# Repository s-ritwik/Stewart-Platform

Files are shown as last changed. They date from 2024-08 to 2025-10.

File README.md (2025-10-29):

# Ship Motion Mimicking and Self-Stabilizing Platform Project


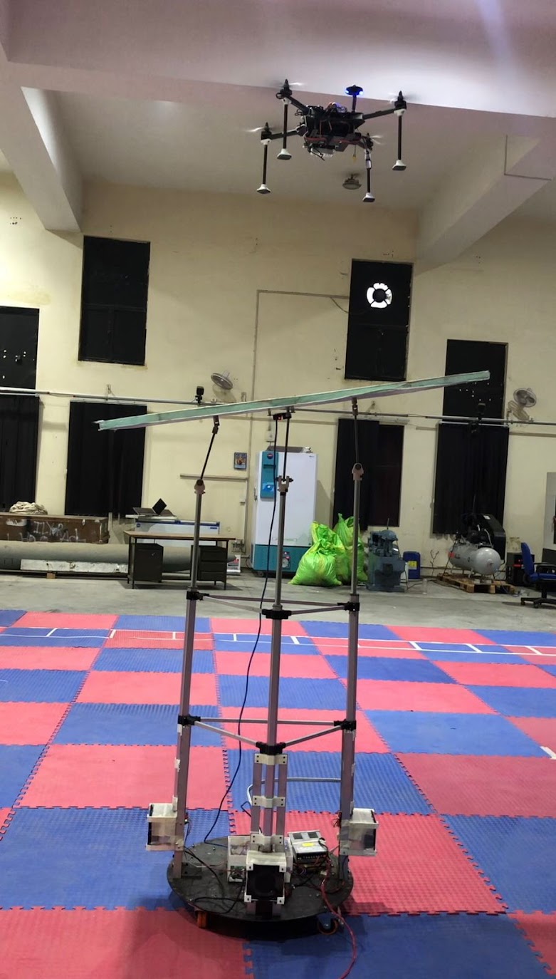
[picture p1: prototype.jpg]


## Overview
This is my undergraduate project aimed at mimicking ship motion and developing a self-stabilizing platform. The project focuses on accurately replicating the dynamic movements of a ship and ensuring that the platform remains stable under various simulated conditions.

## Project Components
- **Ship Motion Mimicry**: Implementing algorithms to replicate the motion dynamics of a ship.
- **Self-Stabilizing Platform**: Designing and testing a platform that can counteract motion to remain stable.
- **CAD Models**: Detailed CAD models of the platform and associated components are available for reference.

## Available Resources
- **[Project Report](Stewart_Platform_1.pdf)**: A comprehensive report detailing the project’s objectives, methodologies, and results.
- **[CAD Models](CAD2.0)**: Access the CAD models used in this project.

## Future Updates
The final pipeline, including Arduino/Raspberry Pi integration, will be posted soon after concluding all tests.

## How to Contribute
Contributions are welcome! Feel free to fork the repository and submit pull requests. If you have any questions or suggestions, please open an issue.

## License
This project is licensed under the Apache License - see the [LICENSE](LICENSE) file for details.

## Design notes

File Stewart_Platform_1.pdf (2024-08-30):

# Project Report:Design and fabrication of Stewart platform for Testing of UAV Ship Deck Landing

Abhishek∗

, Ritwik Shankar†

, Jitendra Singh‡

I. Nomenclature
R | = Radius of the stewart platform
Z | = Heave value considered from ground point
la | = Deflection of the aft actuator from ground point
l f | = Deflection of the forward actuator from ground point
ll | = Deflection of the lateral actuator from ground point
θ | = Pitch deflection of the platform along y axis
φ | = Roll deflection of the platform along x axis
ax | = Raw acceleration data along x axis from MPU6050
ay | = Raw acceleration data along y axis from MPU6050
az | = Raw acceleration data along z axis from MPU6050

θ

accel = Pitch deflection from acceleration data
φ
accel | = Roll deflection from acceleration data
wx | = Angular velocity along x axis
wy | = Angular velocity along y axis
wz | = Angular velocity along z axis
α | = Complimentary filter value

II. Introduction

A. Problem Statement
The challenge of landing a rotor-craft on the deck of a moving ship presents a complex problem that requires precise piloting skills and specialized training. The continuous pitching and rolling of the ship’s deck, driven by ocean swells and winds, creates an inherently unstable landing platform that challenges the pilot’s ability to time the touchdown precisely. The limited physical dimensions of the ship’s deck provide a little margin for error, requiring the pilot to execute the landing manoeuvre with exceptional precision within the constrained spatial envelope. The airflow patterns around the ship’s superstructure and the interaction with the surrounding marine environment can result in turbulent and unpredictable wind conditions, further complicating the pilot’s control inputs.
Successful ship deck landings demand the ability to accurately anticipate the ship’s motion and synchronize the aircraft’s descent. This requires specialized skills, such as precise control inputs to compensate for platform instability, keen situational awareness to monitor the landing environment, and rapid decision-making to address unexpected events. In this paper we investigate a solution to these problems by using vision based estimation of the ship deck platform then a landing algorithm which achieves precision landing on a rolling and pitching platform. To solve this problem, a control algorithm was developed using position estimates from computer vision data. To test the algorithm, a Parallel manipulator was developed, which can accurately simulate ship motions such as roll, pitch and heave, giving a 3-DOF motion to the landing plate. This type of parallel manipulator is known as a Stewart Platform.
B. Literature Review
Ready-made Stewart Platforms were inquired about, but those that fit our requirements were priced above INR 40 Lakhs. Consequently, creating an in-house alternative to cater to our required ship motions became necessary. The

∗Professor, Aerospace Engineering, Indian Institute of Technology Kanpur, Uttar Pradesh, India, 208016, AIAA Member
†Under-Graduate Student, Aerospace Engineering, Indian Institute of Technology Kanpur, Uttar Pradesh, India, 208016
‡Senior Project Executive Officer, Aerospace Engineering, Indian Institute of Technology Kanpur, Uttar Pradesh, India, 208016 dynamics of a Stewart platform were explored through the examination of two sources ([1] & [2]). These sources were consulted to gain insight into the mechanics and functioning of the Stewart platform

III. Ship Deck Simulation Platform

A. Introduction to Stewart Platform
A Gough-Stewart platform was planned to replicate the scone ocean dataset. The anticipated versatility of the Stewart platform for stabilizing ships at sea is illustrated in Fig. 1.

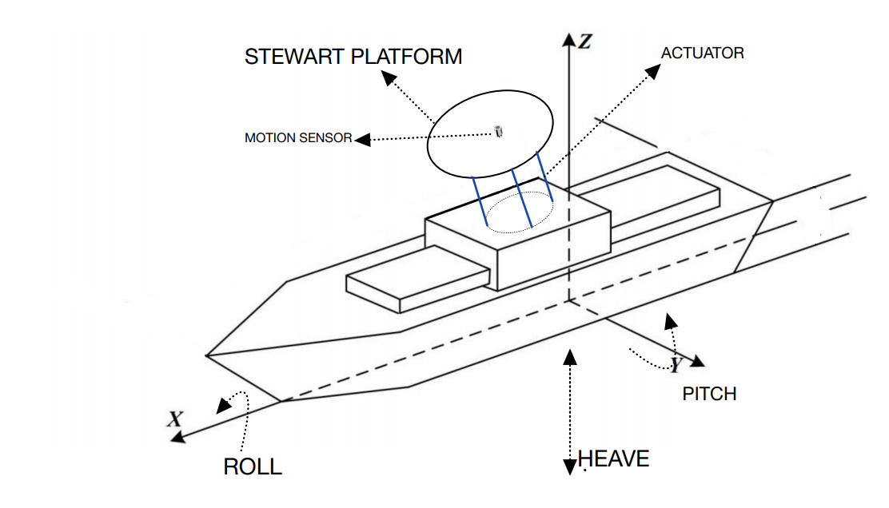
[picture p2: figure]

Fig. 1 The broad applicability of the Stewart platform for stabilizing ships at sea.

Rather than stabilizing the shipboard directly, in our experiment experimentally taken ship data [3] was inputted into the platform to simulate ship conditions at sea state 4 [4].
The aim was to simulate roll(φ),pitch(θ) and heave(Z) motions to test the landing algorithm, as these are the most significant motions captured in the scone dataset; other motions in the plane of the ocean can be mimicked by keeping the platform on a car, which can move in the two perpendicular directions on the ground and also rotate around the axis perpendicular to the plane. Existing market platforms, albeit with a higher frequency operating range, were priced at over 40 Lakhs INR. Hence, there was a significant demand for a cost-effective alternative to a Stewart platform capable of generating the desired motions at a lower frequency of approximately 10 Hertz.
The SCONE dataset [3], acquired through experimentation, was slated for simulation. This dataset comprises two distinct types of data: one predominantly influenced by roll and the other by heave. It is structured as a MATLAB variable containing 36,000 data points, with a time interval of 0.05 seconds between consecutive points. Our research focuses on testing our algorithm using both the roll-dominated and Heave-dominated subset of this dataset (‘SCONE_D3R_1‘ and ‘SCONE_D3H_1‘), where ‘Rot_X‘ represents roll, ‘Rot_Y‘ represents pitch, and Z represents heave. The deck is situated 15 feet (Z = -15 feet) above sea level (Z = 0). The data which is to be simulated is shown in Fig. 2.

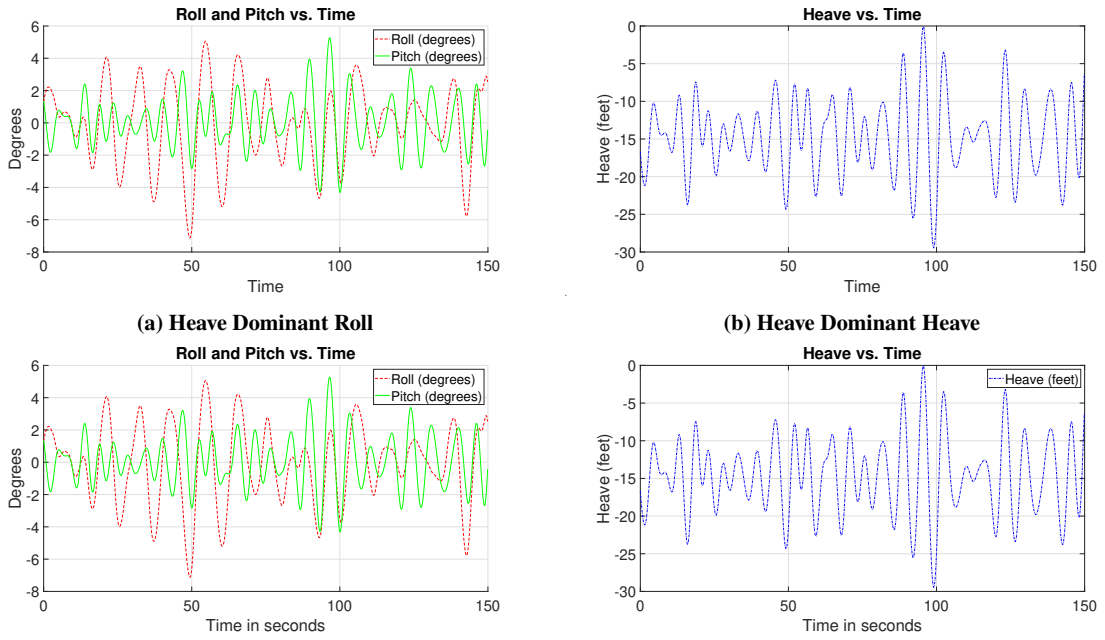
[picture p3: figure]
Time; Degrees; Roll and Pitch vs. Time; Roll (degrees) Pitch (degrees); (a) Heave Dominant Roll; Heave (feet); Heave vs. Time; (b) Heave Dominant Heave; Time in seconds

(c) Roll Dominant Roll
(d) Roll Dominant Heave

Fig. 2 Comparison of Heave and Roll Dominant Parameters

B. Kinematics of the 3-legged platform

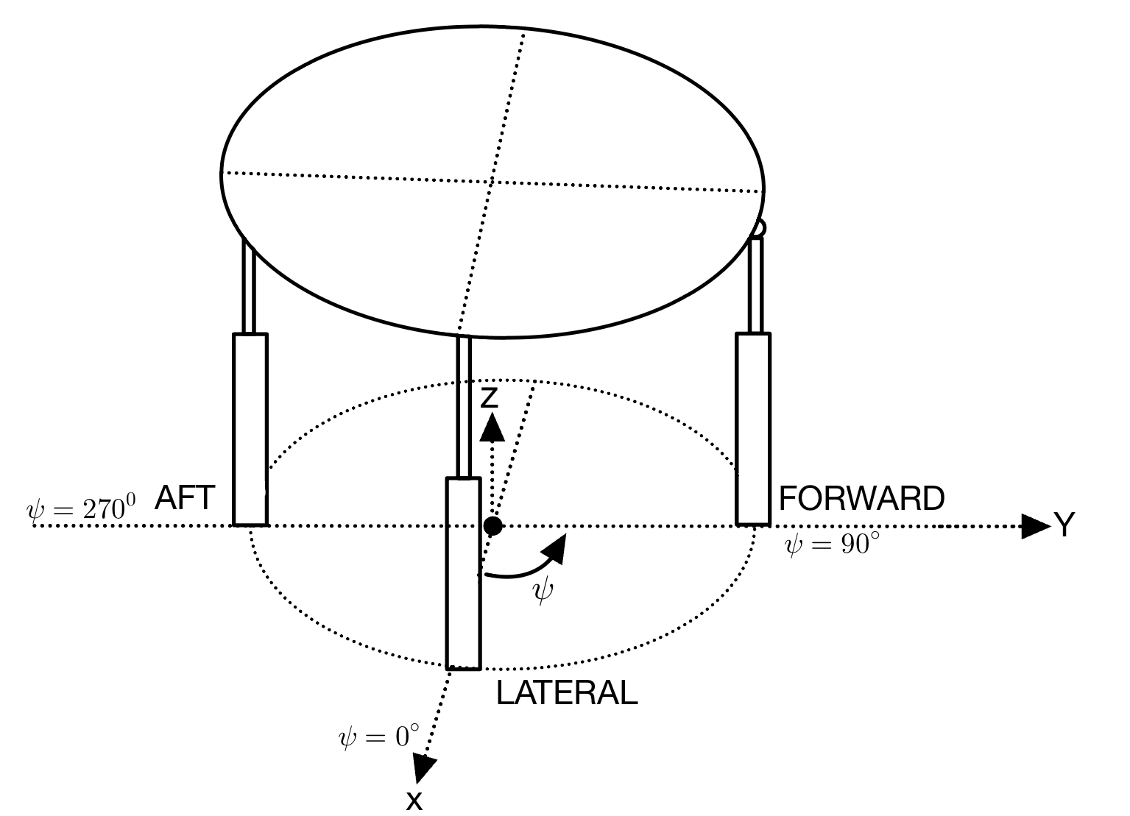
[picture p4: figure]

Fig. 3 Proposed design of the model

Given that actuators constituted the majority of the cost, reducing their number was crucial. Drawing inspiration from UH-60A swashplate [5], a 3-actuator model was chosen for the platform. Since the design drew inspiration from a swashplate, a similar naming convention was adopted for the three actuators: ’lateral’, ’aft’, and ’forward’. In this configuration (Fig. 3), the lateral actuator generates pitching movement, while the aft and forward actuators produce rolling movement.

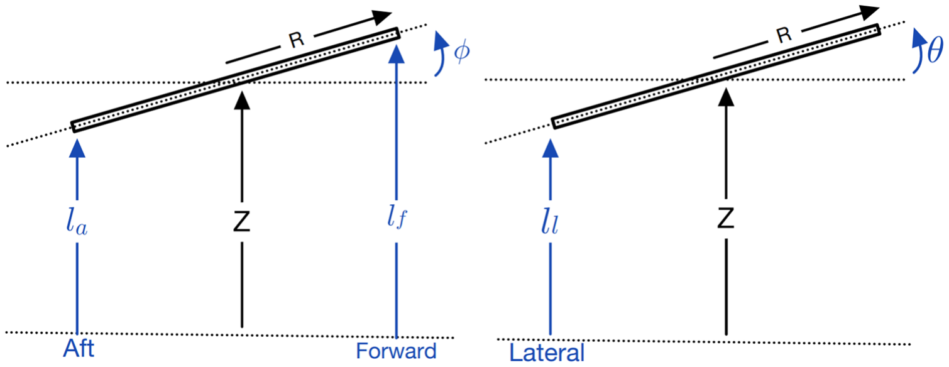
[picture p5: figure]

Fig. 4 Deflection diagram of the system

The inverse kinematics (Fig.4) of the system were solved to determine the necessary movements (Eq. 1) of the actuators to achieve the desired roll, pitch, and heave motions. This process allowed for precise control over the platform’s movements to accurately simulate the conditions needed for testing the landing algorithm.

la = Z − R sin(φ) AFT
l f = Z + R sin(φ) | FORWARD
ll = Z − R sin(θ) | LATERAL

(1)

C. Design of the platform
The decision was made to combine a hinge joint and a universal joint instead of using a three-degree-of-freedom ball joint to allow the top plate to rotate freely around the two desired axes while ensuring it can withstand significant loads. This resulted in adopting a linear actuator-hinge joint-universal joint setup, with the universal joint affixed to the top plates for all three actuators. Mechanical components were carefully chosen based on their functionality and cost considerations.
A linear actuator with an optical encoder to get deflection was chosen with a 6-inch stroke length to accommodate the needs of roll, pitch and heave adequately. The linear speed was 2 inches per second with a load capacity of 36 pounds(16.32 Kg) and a backtracking limit of 200 pounds(90.71 Kg) powered by a 12V SMPS box for power supply. The distance of the three actuator cuts from the centre was 30 cm, which could give us a deflection of approximately 10 degrees in under a second.
Keeping these configurations in mind, a CAD model was created for precision plasma cut for the base plate of the platform so that the actuators can be fixed on the base plate (Mild steel) with precision.

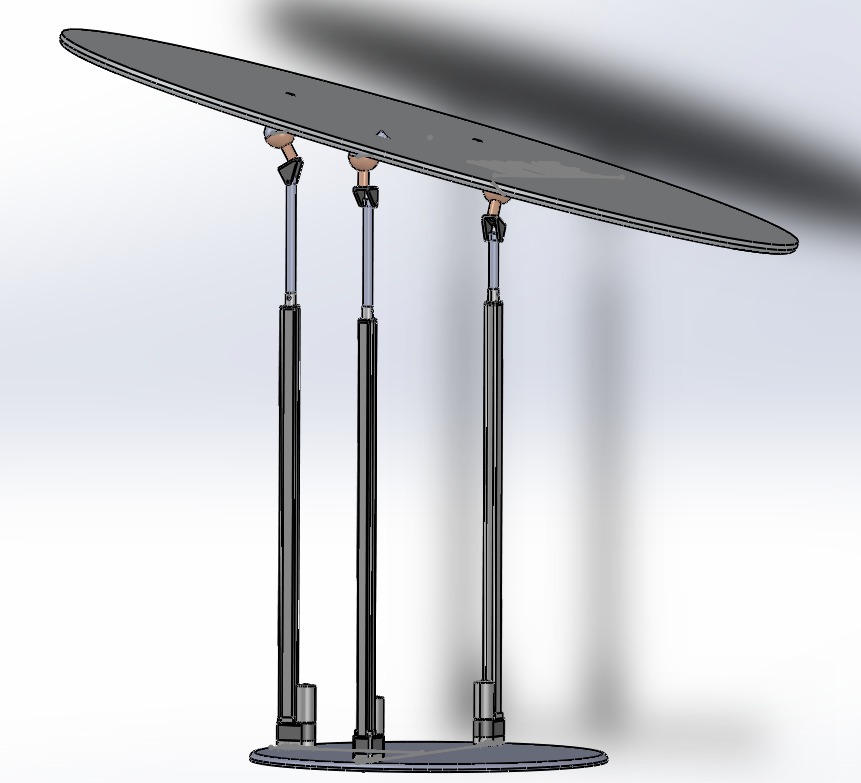
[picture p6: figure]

Fig. 5 Platform’s final Configuration

D. State estimation & Controller design
The MPU6050 IMU sensor was utilized to capture raw acceleration and gyroscope data from the platform.It was attached at the centre of the top plate of the platform. The accelerometer and gyroscope biases are calculated as zero offsets by keeping the IMU stationary and flat on level ground. For the scale factor of the accelerometer, we solve the system of linear equations for three known orientations. As described in ([6]) the euler angles, roll(φ) and pitch(θ) from acceleration readings are calculated as follows:

φ

accel = tan−1

ay

az

(2)

θ

accel = tan−1

−ax
√︁
(ay)

2 + (az )

2

!
(3)

Before discussing the calculation of the final euler angles, it is important to understand the context and objectives of our data collection methods.
- Gyroscope data furnishes rapid response and high-frequency details regarding orientation changes, albeit prone to drift over time.
- Accelerometer data delivers precise insights into gravity’s direction but is vulnerable to noise and inaccuracies in an actuated system, particularly during motion.
Employing a blending factor of 0.9, the complementary filter ([7]) combines the gyroscopic and acceleration data to compute the final pitch and roll values. At each iteration, a new roll(Eq.4) and pitch(Eq.5) are determined, factoring in the difference in time (dt) between consecutive iterations.

φ = α · (φ + wx · dt) + (1 − α) · φ

accel | (4)

θ = α · (θ + wy · dt) + (1 − α) · θ

accel | (5)

The Heave calculation for the platform is determined by pose estimation using an ArUco marker and a webcam. The control architecture of the full system is given in Fig. 6

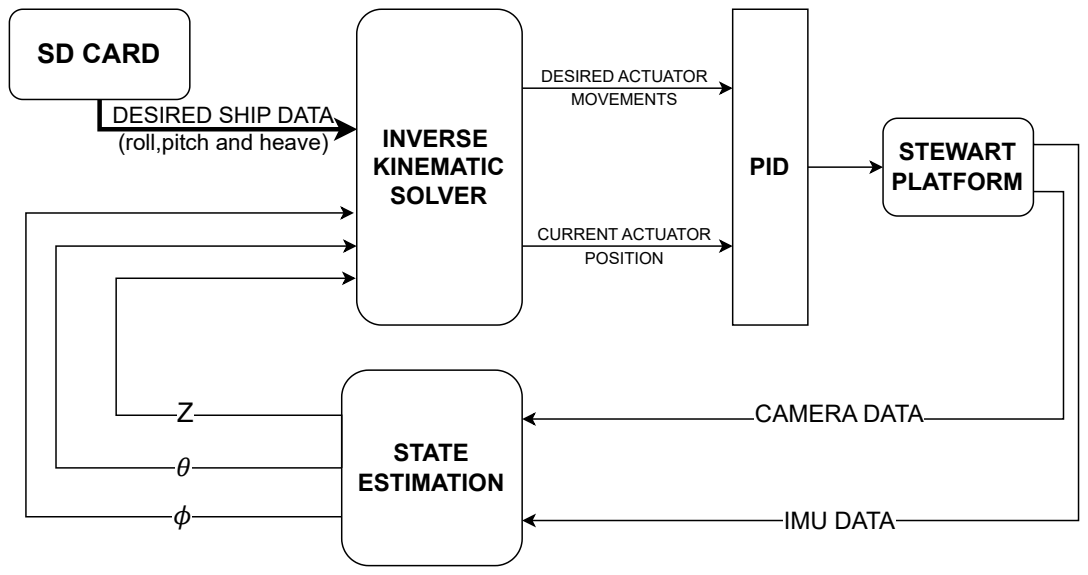
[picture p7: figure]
SD CARD; DESIRED ACTUATOR; INVERSE KINEMATIC SOLVER; IMU DATA; CAMERA DATA; STEWART PLATFORM; STATE ESTIMATION; PID; MOVEMENTS; CURRENT ACTUATOR POSITION; DESIRED SHIP DATA (roll,pitch and heave)

Fig. 6 Control architecture of the system

E. Hardware Implementation

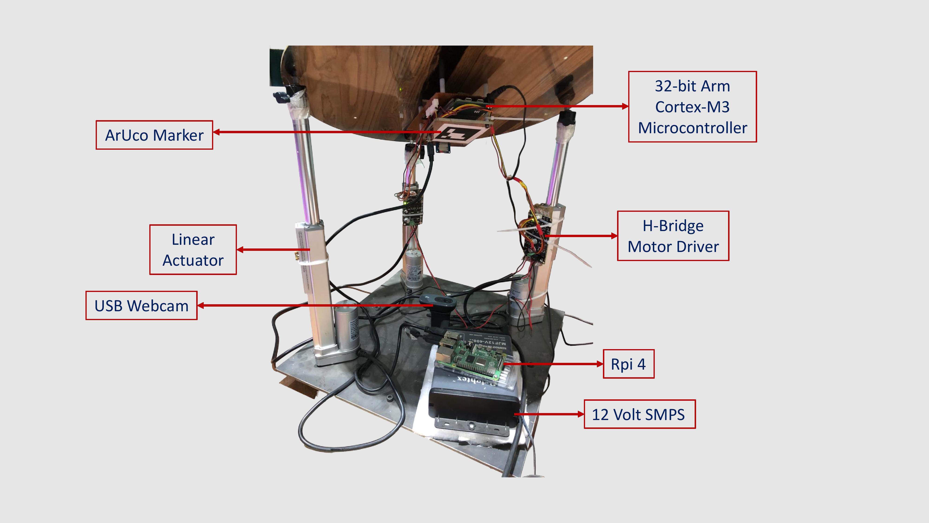
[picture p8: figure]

Fig. 7 Electronic components of the system

The platform’s electronics, illustrated in Fig. 7, includes an MPU6050 sensor, which collects raw accelerometer and gyroscopic data and transmits it to an Arduino Due microcontroller based on the 32-bit Atmel SAM3X8E ARM Cortex-M3 CPU. This microcontroller performs inverse kinematics calculations and controls the linear actuators to achieve the desired lengths using the Cytron Dual Channel Enhanced 10Amp DC Motor Driver 30A Peak MDD10A, which features an H-bridge and is powered by a 12 Volt 100A SMPS board. A Quad-core Cortex-A72 (ARM v8) 64-bit Raspberry Pi 4 processes ArUco marker data from a USB webcam to determine the distance from the bottom plate to the board (Z, or heave) and receives Qualisys motion capture data via a master-slave link, with the Qualisys system as the master and the Raspberry Pi 4 as the slave. An SD card provides the microcontroller with reference ship sea state data and logs the resulting platform data. The overall hardware architecture of the platform is detailed in Figure 8.

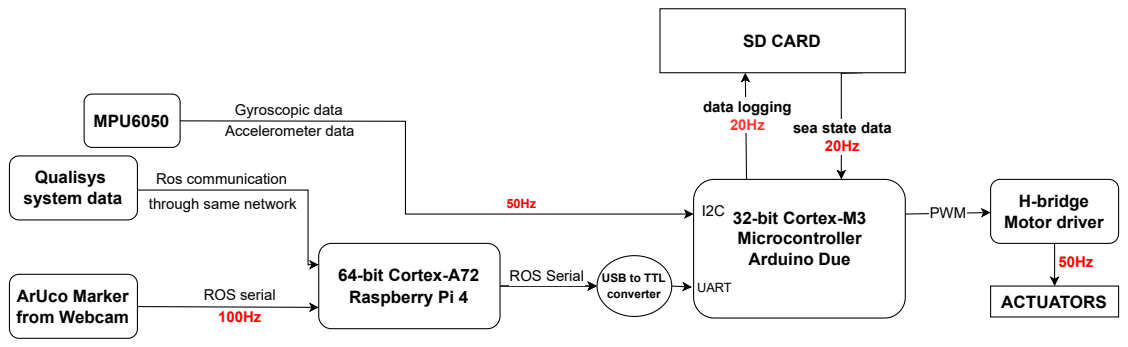
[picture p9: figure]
32-bit Cortex-M3; PWM; Microcontroller Arduino Due; H-bridge Motor driver; sea state data 20Hz; SD CARD; data logging 20Hz; Gyroscopic data Accelerometer data; MPU6050; 64-bit Cortex-A72 Raspberry Pi 4; USB to TTL converter; Qualisys system data; ArUco Marker from Webcam; ACTUATORS; ROS Serial; UART; Ros communication; through same network; ROS serial 100Hz

Fig. 8 Hardware architecture of the system

F. Results

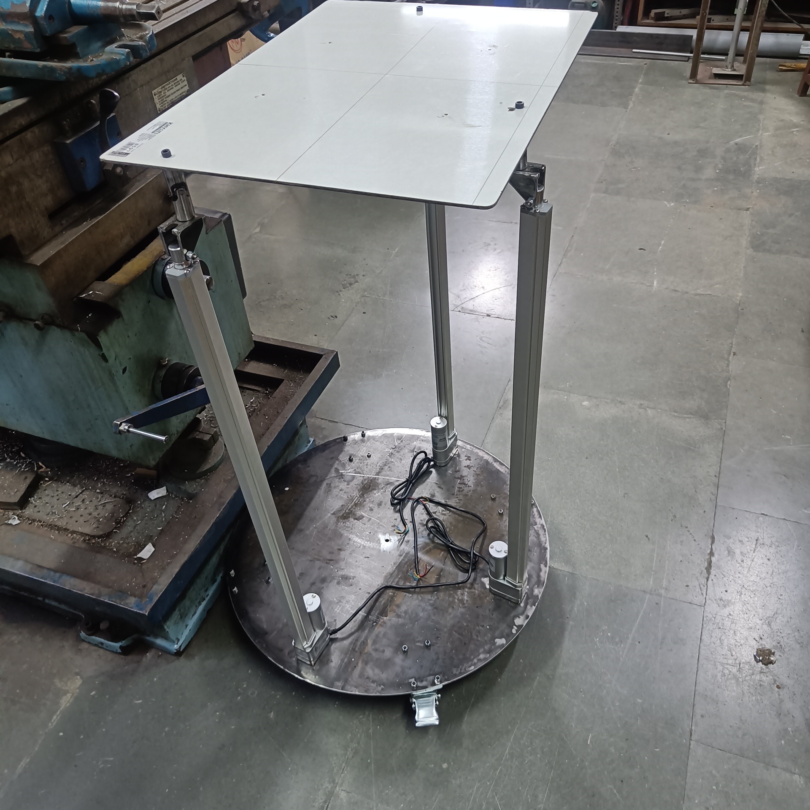
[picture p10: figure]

Fig. 9 Stewart Platform Assembly

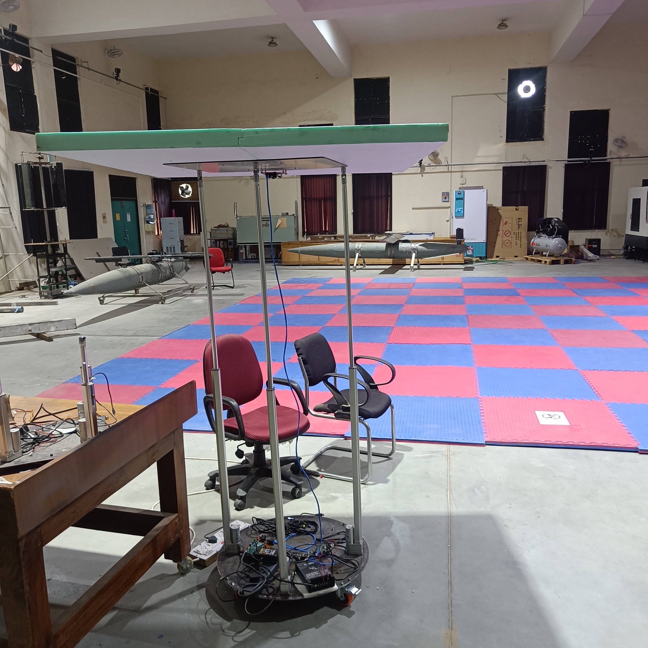
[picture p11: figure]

Fig. 10 Final Stewart Platform

The base plate was constructed and actuators were assembled (Fig. 9), with a top plate made of XPS foam board attached to the three actuators, chosen for its lightweight properties and minimal bending, which helps reduce vibrational noise affecting the IMU sensor. A Qualisys motion capture system was set up, and five super spherical markers were placed on the platform for accurate motion tracking. The final setup is illustrated in Fig. 10.
To evaluate the platform’s functionality, the Scone dataset was loaded onto the platform. The tracked values from the IMU, ArUco marker, and motion capture system were compared against the reference values for the roll(Fig. 11). Additionally, the sinusoidal data tracked by the ArUco marker and motion capture system was compared to the reference values for heave(Fig. 12).

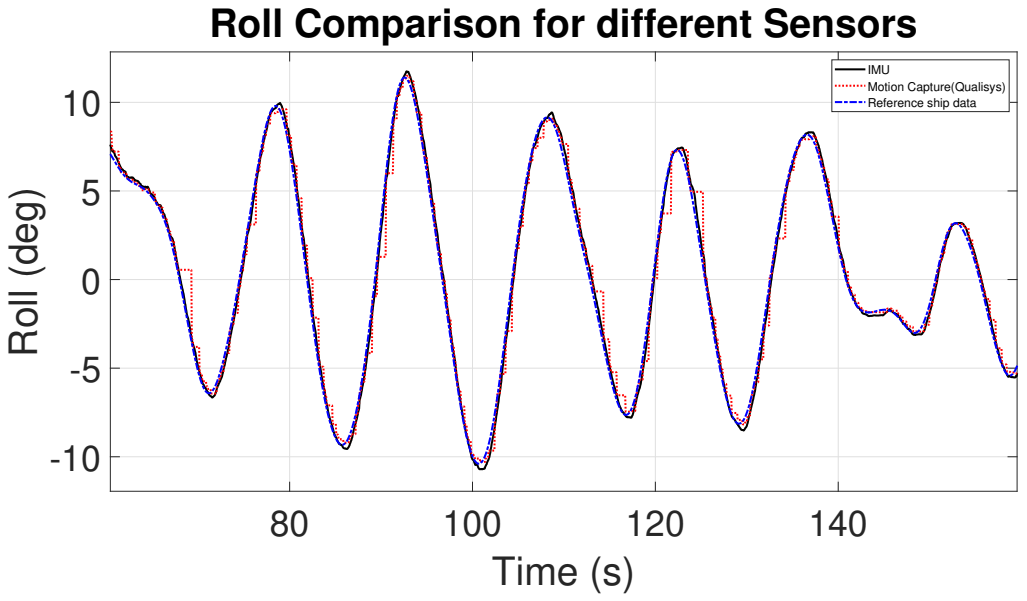
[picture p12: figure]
Time (s); Roll (deg); Roll Comparison for different Sensors; IMU Motion Capture(Qualisys) Reference ship data

Fig. 11 Roll data performance of the platform

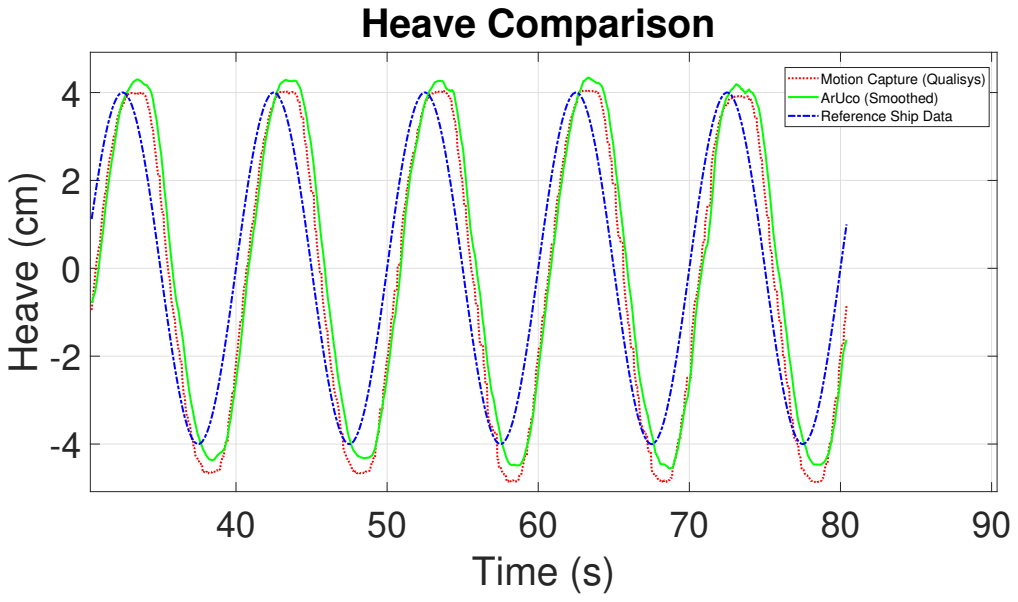
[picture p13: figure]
Time (s); Heave (cm); Heave Comparison; Motion Capture (Qualisys) ArUco (Smoothed) Reference Ship Data

Fig. 12 Heave data performance of the platform

IV. Future Work

A. Linear Speed
The first iteration model was successfully able to cater for the needs of Roll/Pitch or Heave, but when all three motions were combined, it was not able to follow the data with the precision that we wanted.So, increasing the speed of the linear actuators was necessary. The faster motors, which is rated for 22 Volts, have been ordered, and the gear assembly of the Linear actuator has been changed by using a custom 3D Printed Gear assembly and increasing the ratio from the initial 5:1 to 1:1.6, increasing the speed 8.33 times. We expect a further increase in linear speed after replacing the actuator motors. The motors have arrived and the final assembly is to be completed by 10th August.
B. Additional Degrees of Freedom
To test the algorithm for a more realistic condition, additional movements of Sway are to be added as well,this will be achieved by TO BE ADDED

References
[1] Staicu, S., “Dynamic analysis of the 3-3 Stewart platform,” UPB Scientific Bulletin D, Vol. 71, No. 2, 2009, pp. 3–18.
[2] Abedinnasab, M. H., Yoon, Y.-J., and Zohoor, H., “Exploiting higher kinematic performance-using a 4-legged redundant PM rather than gough-stewart platforms,” Serial and Parallel Robot Manipulators-Kinematics, Dynamics, Control and Optimization, Vol. 10, 2012, p. 32141.
[3] Schwartz, A., “Systematic Characterization of the Naval Environment (SCONE) - Standard Deck Motion Data for a Generic Surface Combatant,” [Online]. Available: http://www.navalengineers.org/Symposia/PastSymposia/Launch-and-Recovery-2016/Program/Schwartz, (http://www.navalengineers.org/Symposia/PastSymposia/Launch-and-Recovery-2016/Program/Schwartz) 2015.
[4] Owens, E. H., SEA CONDITIONSDouglas scale; Peterson scale; Sea stateSea conditions, Springer US, New York, NY, 1984, pp. 722–722. https://doi.org/10.1007/0-387-30843-1_397, URL https://doi.org/10.1007/0-387-30843-1_397.
[5] Abhishek, A., Datta, A., and Chopra, I., “Prediction of UH-60A structural loads using multibody analysis and swashplate dynamics,” Journal of aircraft, Vol. 46, No. 2, 2009, pp. 474–490.
[6] Kharolia, D., Singh, J., and Kothari, M., “Autopilot Design and Development for Multirotor UAVs,” AIAA SCITECH 2024 Forum, 2024, p. 1698.
[7] Van de Maele, P.-J., “Reading a imu without kalman: The complementary filter,” Pieter-Jan. com Creaty in Automation y More, Vol. 26, 2013.

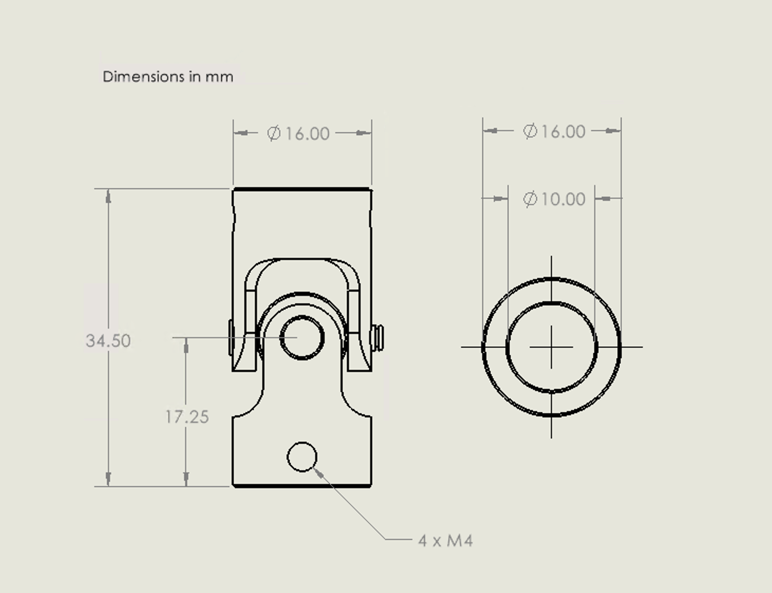
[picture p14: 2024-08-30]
CAD2.0/universal/Images/dimensions.png

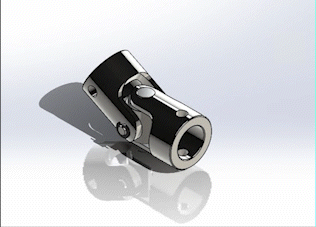
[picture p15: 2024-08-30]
CAD2.0/universal/Images/exploded.gif

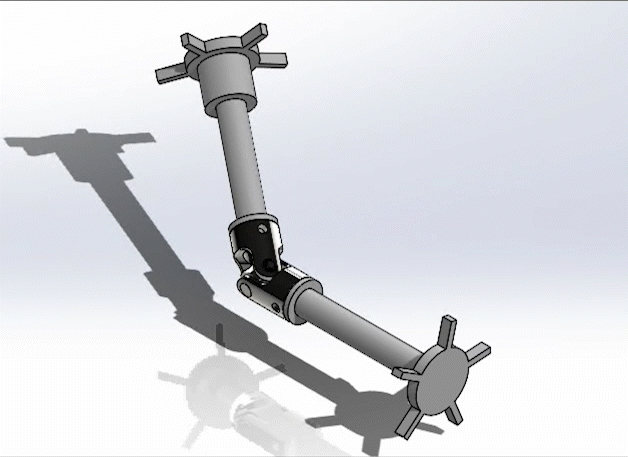
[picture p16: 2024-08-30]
CAD2.0/universal/Images/action.gif

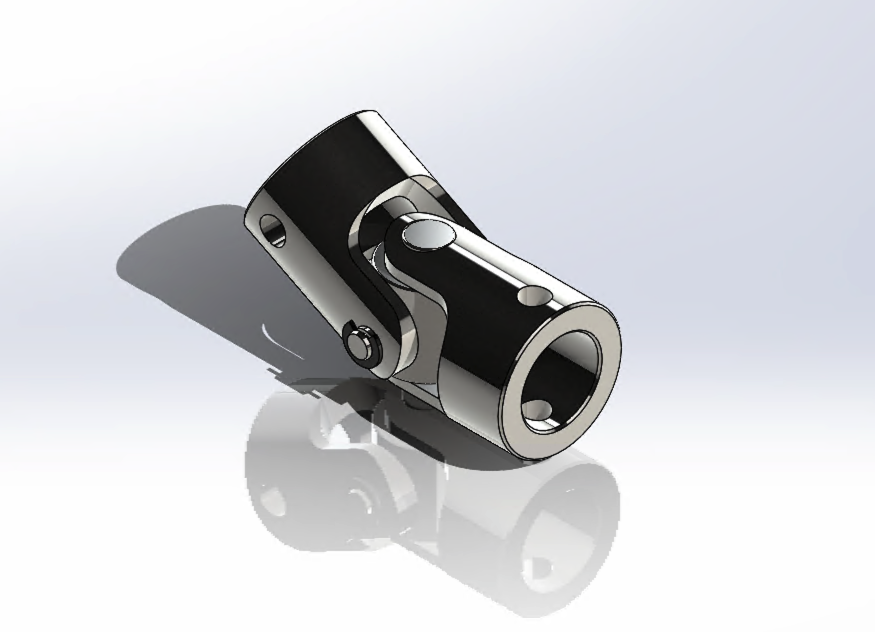
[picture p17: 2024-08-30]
CAD2.0/universal/Images/CAD.png

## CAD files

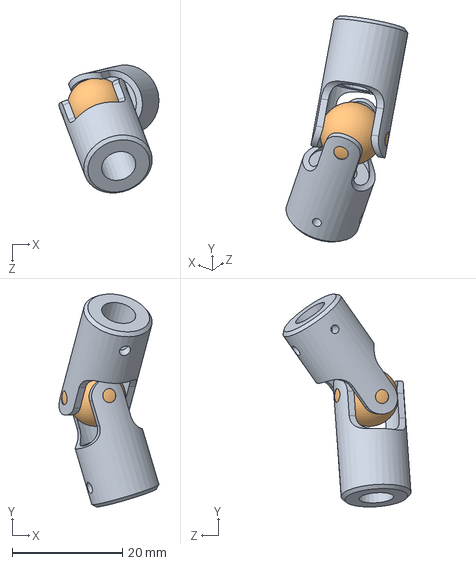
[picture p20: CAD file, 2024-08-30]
CAD2.0/uni/ASSY_BERG_UJ3_U-JOINT_0250 SHAFT.sldasm
18.1 x 38.6 x 23.1 mm
UJ-3_YOKE x 2
UJ-3_BALL

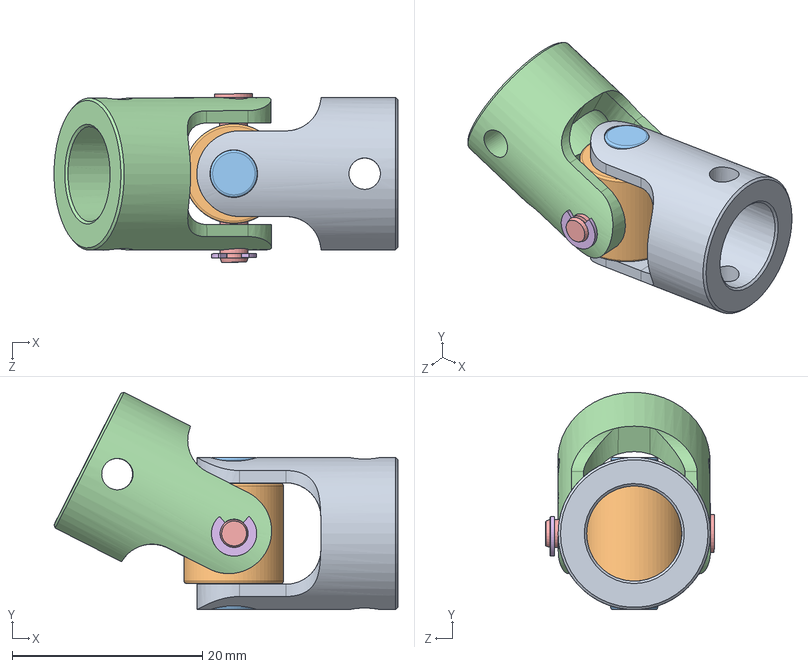
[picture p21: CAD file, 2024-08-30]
CAD2.0/UniversalJoint_10x10mm.SLDASM
36.1 x 22.8 x 17.7 mm
ForkA
Center
PinA
ForkB
PinB
Tab

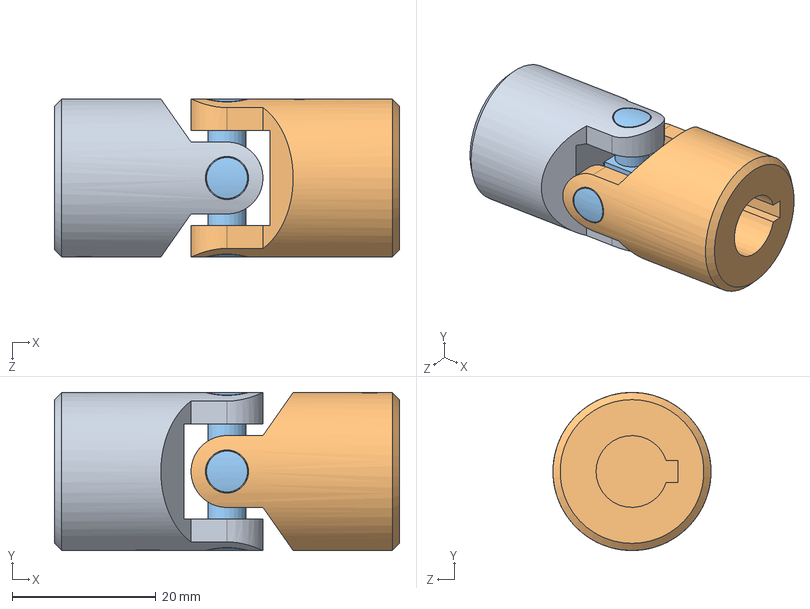
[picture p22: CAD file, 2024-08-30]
CAD2.0/03H-N_assembly/T.E.A. Transmissions Pty Ltd - Australia b65f3cdd-ef4a-384b-a0e4-523af0b97be2.SLDASM
48.0 x 22.0 x 22.0 mm
03h-n_01
03h-n_02
03h-n_03

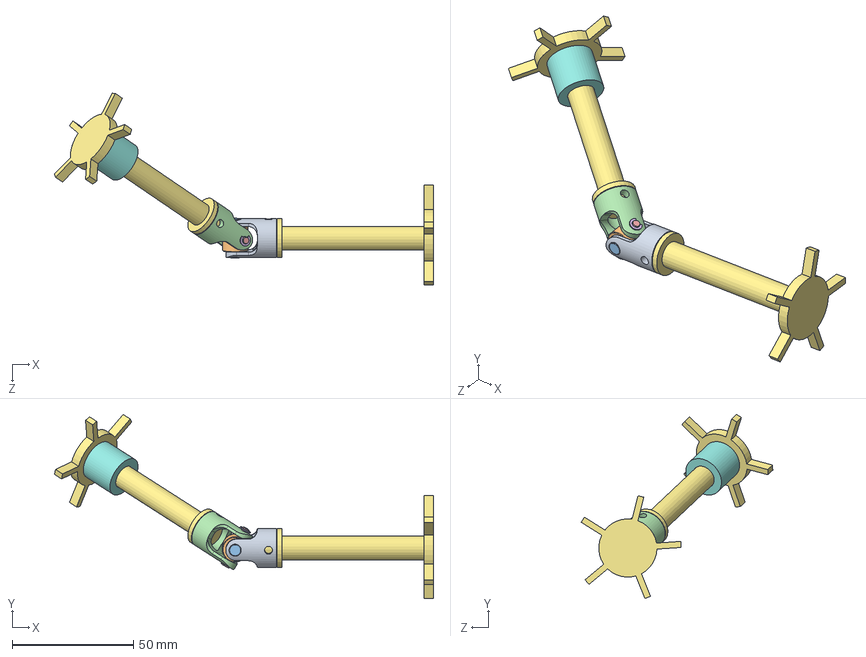
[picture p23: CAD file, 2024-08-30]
CAD2.0/universal/SolidWorks/Sample Assembly/SampleAssembly.SLDASM
156.2 x 75.9 x 79.0 mm
ForkA
Center
PinA
ForkB
PinB
Tab
SampleRod x 2
SampleCoupling

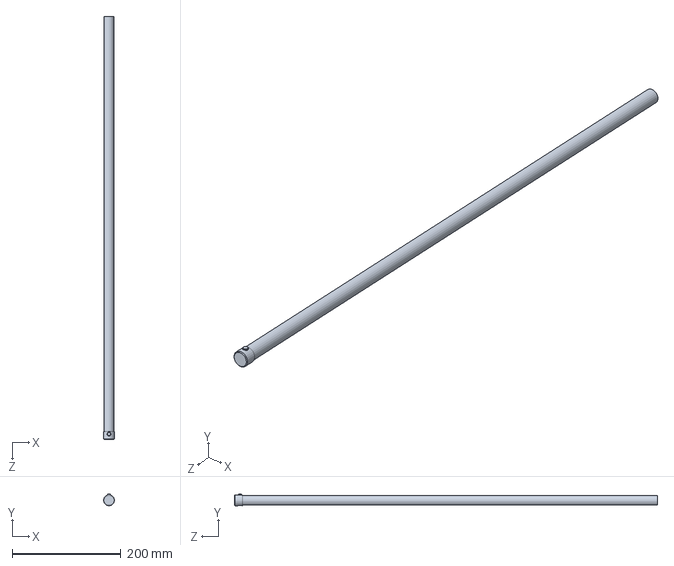
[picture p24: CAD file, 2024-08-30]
CAD2.0/actuator_rod.SLDPRT
20.0 x 21.2 x 776.6 mm

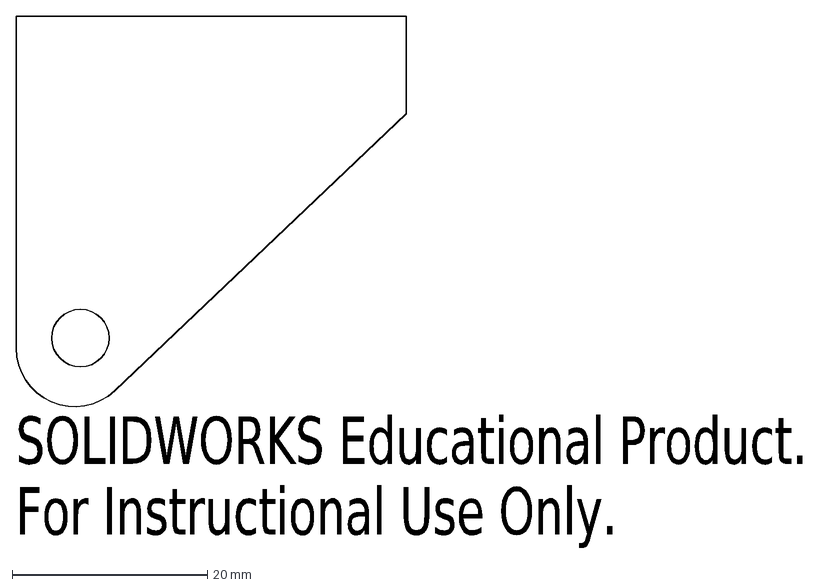
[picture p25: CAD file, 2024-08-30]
CAD2.0/Dxf_files/bracketside.DXF
SOLIDWORKS Educational Product.
For Instructional Use Only.

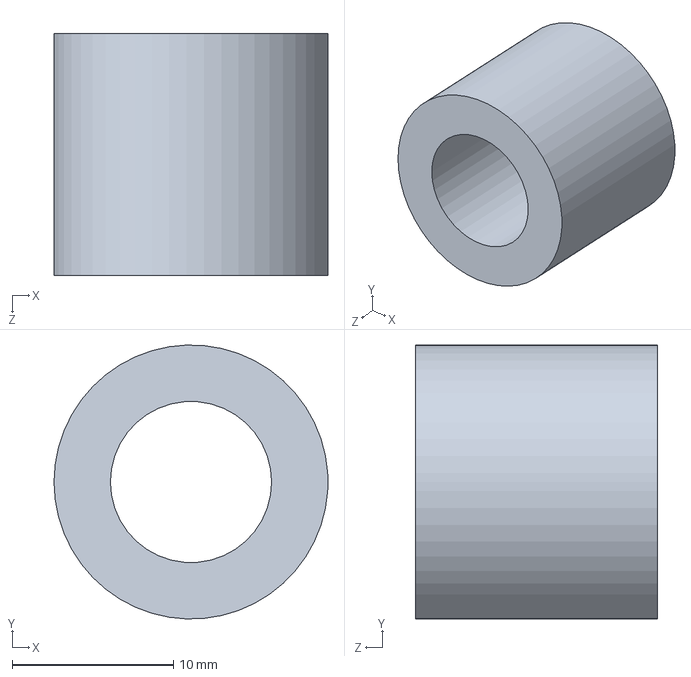
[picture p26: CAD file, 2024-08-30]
CAD2.0/universal/SolidWorks/Sample Assembly/SampleCoupling.SLDPRT
17.0 x 17.0 x 15.0 mm

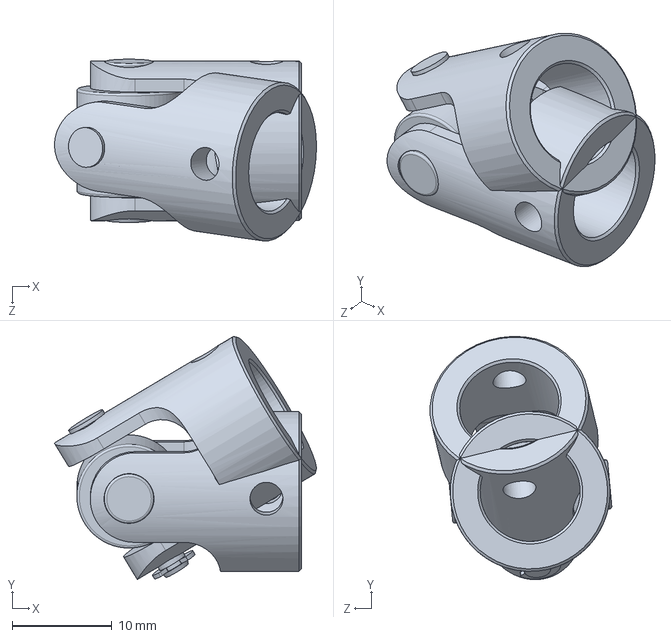
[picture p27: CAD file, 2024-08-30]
CAD2.0/universal/SolidWorks/UniversalJoint_10x10mmpart.SLDPRT
26.2 x 24.3 x 18.2 mm

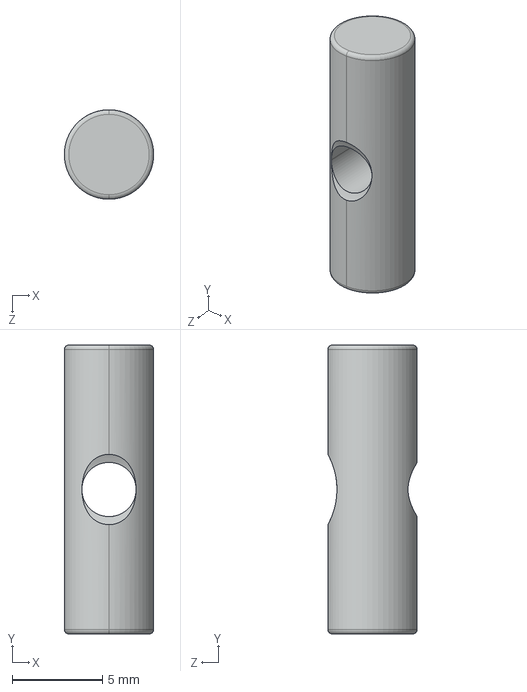
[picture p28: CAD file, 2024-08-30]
CAD2.0/universal/STEP/PinA.STEP
4.95 x 16.0 x 4.95 mm

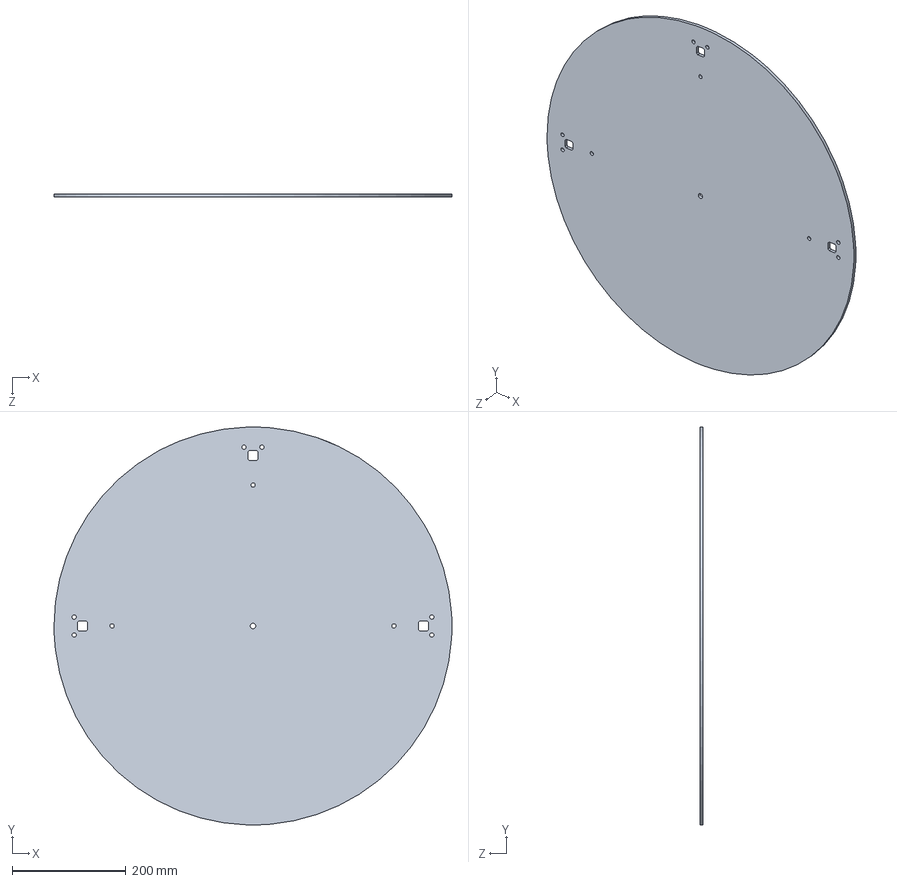
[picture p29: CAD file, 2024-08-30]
CAD2.0/Dxf_files/baseplatefordxf.SLDPRT
700.0 x 699.9 x 6.00 mm

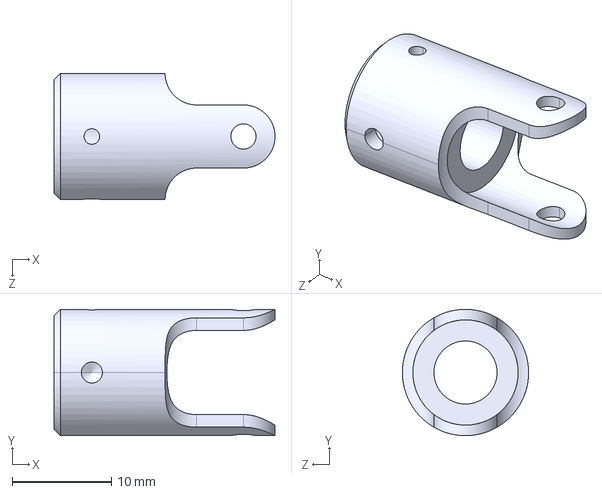
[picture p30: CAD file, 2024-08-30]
CAD2.0/uni/UJ-3_YOKE.STEP
22.2 x 12.7 x 12.7 mm

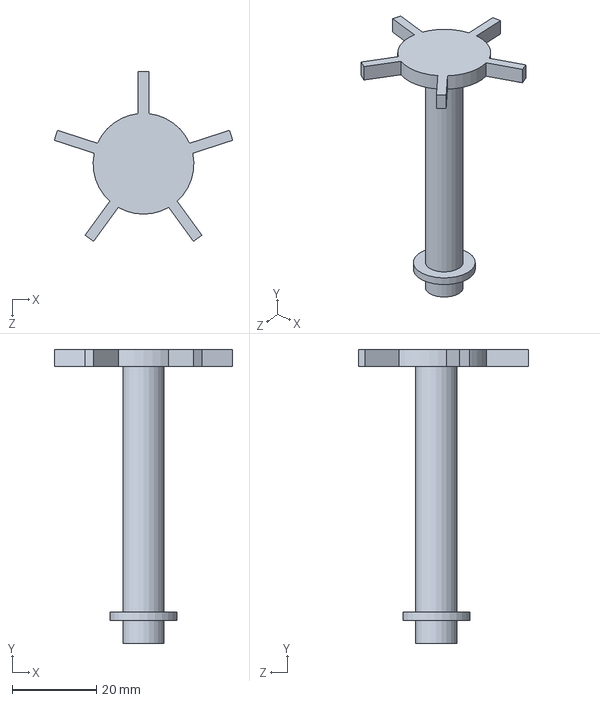
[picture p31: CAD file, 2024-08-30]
CAD2.0/universal/SolidWorks/Sample Assembly/SampleRod.SLDPRT
42.5 x 70.0 x 40.4 mm

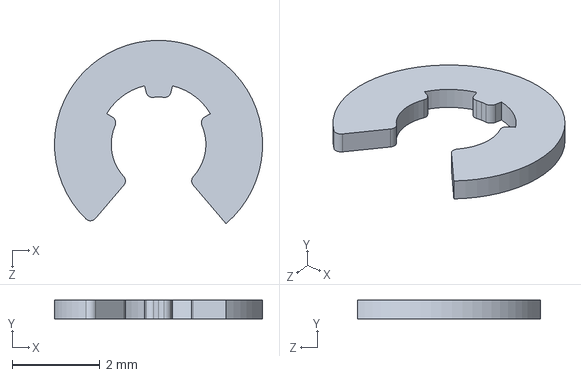
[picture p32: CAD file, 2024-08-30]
CAD2.0/universal/STEP/Tab.STEP
4.75 x 0.425 x 4.18 mm

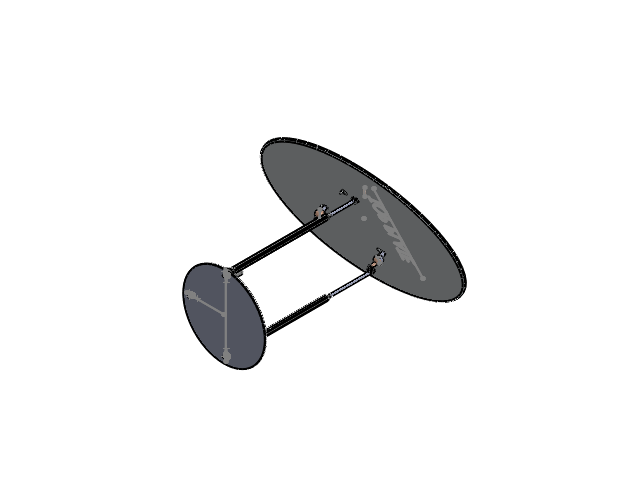
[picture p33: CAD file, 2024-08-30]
CAD2.0/final.SLDASM
baseplate
30inch x 3
actuator_rod x 3
revolute_joiny x 3
part 2 inner x 3
Part1 outer x 3
topplate

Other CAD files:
CAD2.0/uni10.SLDASM
CAD2.0/Assembly.SLDASM
CAD2.0/03H-N_assembly/03h-n_03.SLDPRT
CAD2.0/03H-N_assembly/03h-n_02.SLDPRT
CAD2.0/03H-N_assembly/03h-n_01.SLDPRT
CAD2.0/30inch.SLDPRT
CAD2.0/30inch_actuator - Copy.step
CAD2.0/30inch_actuator.step
CAD2.0/8mm U-Joint.SLDASM
CAD2.0/8mm U-Joint.STEP
CAD2.0/Center.SLDPRT
CAD2.0/Dxf_files/baseplatefordxf.DXF
CAD2.0/Dxf_files/bracket.SLDPRT
CAD2.0/Dxf_files/bracket.step
CAD2.0/Dxf_files/bracketbase.DXF
CAD2.0/ForkA.SLDPRT
CAD2.0/ForkB.SLDPRT
CAD2.0/PinA.SLDPRT
CAD2.0/PinB.SLDPRT
CAD2.0/Tab.SLDPRT
CAD2.0/UniversalJoint_10x10mm.SLDPRT
CAD2.0/actuatormouth.SLDPRT
CAD2.0/baseplate.SLDPRT
CAD2.0/revolute.step
CAD2.0/revolute_joiny.SLDPRT
CAD2.0/topplate.SLDPRT
CAD2.0/uni/UJ-3_BALL.IGS
CAD2.0/uni/UJ-3_BALL.STEP
CAD2.0/uni/UJ-3_BALL.sldprt
CAD2.0/uni/UJ-3_YOKE.IGS
CAD2.0/universal/STEP/Center.STEP
CAD2.0/universal/STEP/ForkA.STEP
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

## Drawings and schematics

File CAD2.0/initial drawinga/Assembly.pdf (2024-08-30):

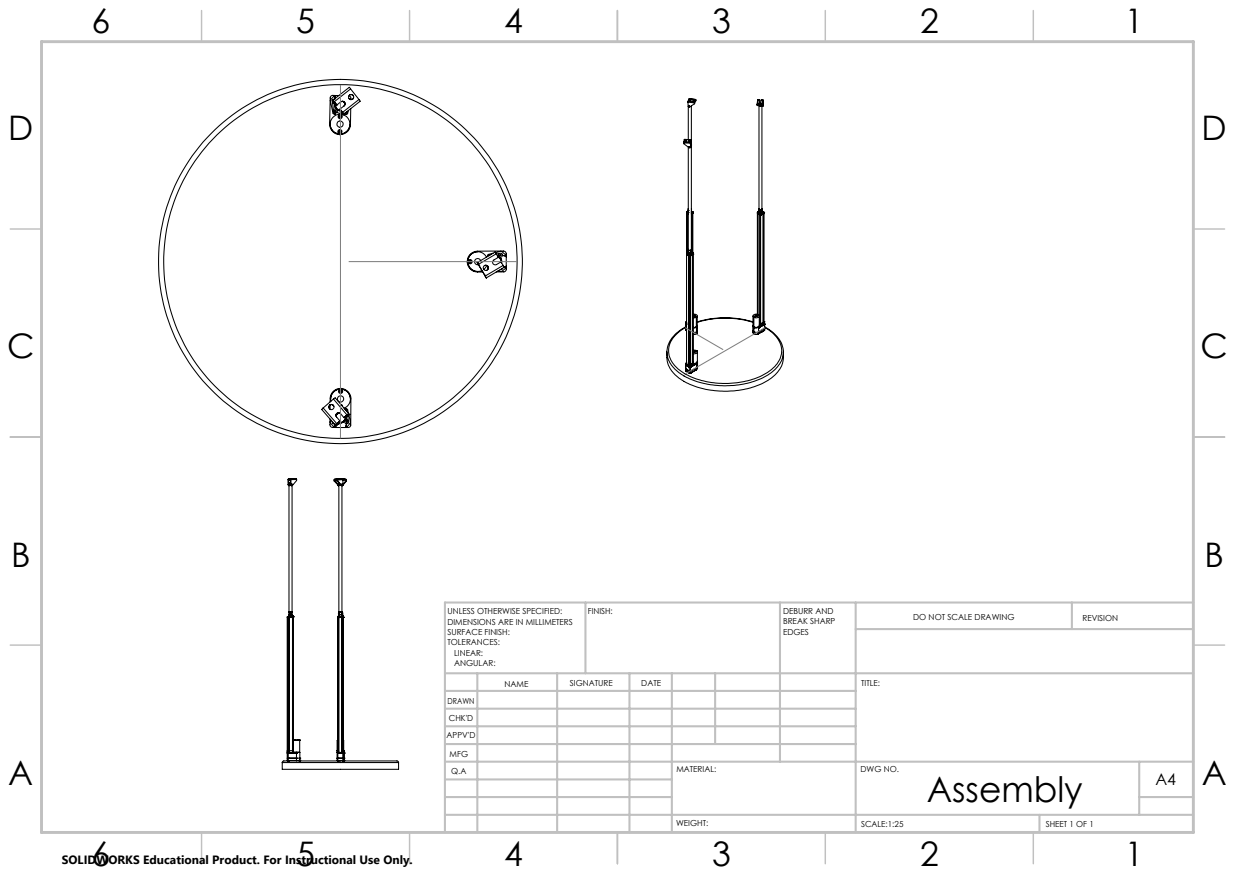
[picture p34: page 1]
FINISH:; DEBURR AND; BREAK SHARP; DO NOT SCALE DRAWING; REVISION; SCALE:1:25; SHEET 1 OF 1

UNLESS OTHERWISE SPECIFIED:
DIMENSIONS ARE IN MILLIMETERS
SURFACE FINISH:
TOLERANCES:
LINEAR:
ANGULAR:

NAME | SIGNATURE | DATE | | | | TITLE:

DRAWN
CHK'D
APPV'D
MFG
Q.A | | | | MATERIAL: | DWG NO. Assembly | A4

SOLIDWORKS Educational Product. For Instructional Use Only.

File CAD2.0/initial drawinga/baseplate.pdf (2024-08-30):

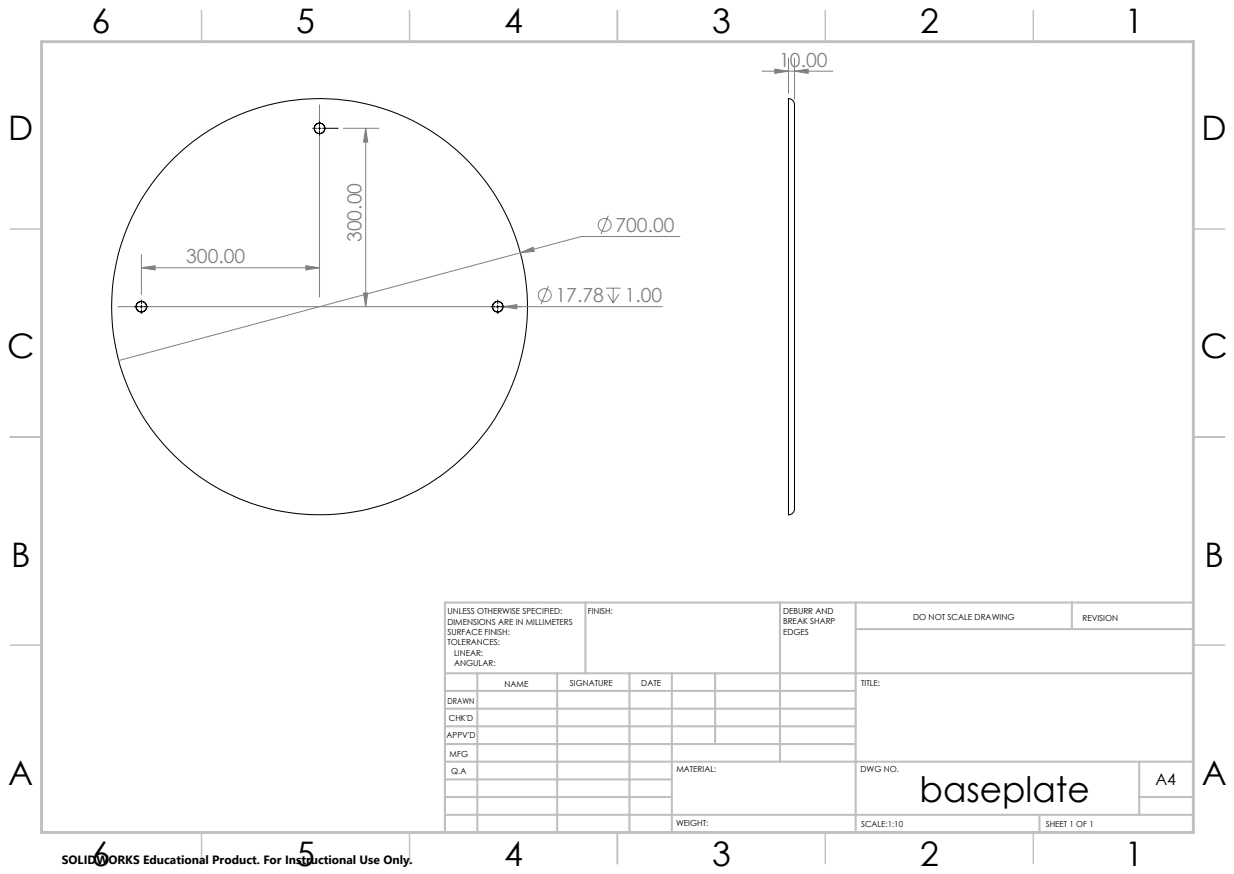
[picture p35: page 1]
FINISH:; DEBURR AND; BREAK SHARP; DO NOT SCALE DRAWING; REVISION; SCALE:1:10; SHEET 1 OF 1

UNLESS OTHERWISE SPECIFIED:
DIMENSIONS ARE IN MILLIMETERS
SURFACE FINISH:
TOLERANCES:
LINEAR:
ANGULAR:

NAME | SIGNATURE | DATE | | | | TITLE:

DRAWN
CHK'D
APPV'D
MFG
Q.A | | | | MATERIAL: | DWG NO. baseplate | A4

SOLIDWORKS Educational Product. For Instructional Use Only.

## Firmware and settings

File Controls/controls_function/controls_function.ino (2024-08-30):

//#include <pidcontroller.h>

// Basic demo for accelerometer readings from Adafruit MPU6050
#include "I2Cdev.h"
#include "MPU6050.h"
#include <Adafruit_MPU6050.h>
#include <Adafruit_Sensor.h>
#include <Wire.h>
#include <math.h>
#include "CytronMotorDriver.h"
#include <stdbool.h>


MPU6050 accelgyro(0x68); // <-- use for AD0 high
Adafruit_MPU6050 mpu;
sensors_event_t a, g, temp;
////////////////////////////////////////////////////////////////////////DEFINE//////////////////////////////////////////////////////////////////////////////////////////////


#define beta 33.56
#define phi (90 - beta)
#define rs 200
#define alpha 0.85
#define DEG_TO_RAD M_PI/180


////////////////////////////////////////////////////////////////////////STRUCTS//////////////////////////////////////////////////////////////////////////////////////////////
CytronMD aft(PWM_DIR, 13,12); 
CytronMD forward(PWM_DIR, 11,10); 
CytronMD lateral(PWM_DIR, 6,5); 

int16_t ax, ay, az,gx, gy, gz;


// Enum to define controller types
typedef enum {
   P_Cont,     // Proportional control only
  PI_Cont,    // Proportional-Integral control
  PID_Cont    // Proportional-Integral-Derivative control
} Mode;


typedef struct {
    /* CONTROLLER GAINS */
    float kp; // Proportional gain
    float ki; // Integral gain
    float kd; // Derivative gain

    /* CONTROLLER OUTPUT LIMIT */
    float U_max; // Maximum output limit
    float U_min; // Minimum output limit

    /* CONTROLLER PARAMETERS */
    float dt;        // Sampling time
    float I;         // Integrator memory
    float state_old; // Old value of state
    float state_f;   // Filter output of actual data
    float fc;        // Gain for low pass filter
    bool enabled;     // Flag to indicate if the controller is enabled
} PIDController;

typedef struct data{
    float x;
    float y;
    float z;
    float bx;
    float by;
    float bz;
  }vec;

typedef struct actu{
    float lateral;
    float aft;
    float forward;
    
  }actuator;

typedef struct s{
  vec accel;
  vec gyro;
  float roll;
  float pitch;
  float roll_acc;
  float pitch_acc;
  float roll_bias=0;
  float pitch_bias=0;
}sensor;

float roll_req=00,pitch_req=0;
 
////////////////////////////////////////////////////////////////////////GLOBAL VARIABLES//////////////////////////////////////////////////////////////////////////////////////////////
float dt=0.01;
double MPUOffsets[6] = { -2752.0/16384, -4504.0/16384, 1615.0/16384, 91, 11, 6 };
sensor imu;
int c=0;
actuator current,required;
  float kd=01,kp=25,ki=0.3;
  PIDController ControlLateral = {kp,ki,kd,255,-255,dt,0,0,0,80,false};
  PIDController ControlAft = {kp,ki,kd,255,-255,dt,0,0,0,80,false};
  PIDController ControlForward = {kp,ki,kd,255,-255,dt,0,0,0,80,false};
////////////////////////////////////////////////////////////////////////FUNCTIONS//////////////////////////////////////////////////////////////////////////////////////////////

// First-order IIR (Infinite Impulse Response) filter
float LPF(float x, float fc, float dt, float yOld) {
    // Precompute the filter coefficient
    float alph = (dt * fc) / (1.0f + dt * fc);

    // Update the filtered output using the precomputed coefficient
    return alph * x + (1.0f - alph) * yOld;
}
/* Saturation function */
float sat(float value, float max, float min) {
    // Ensure that the value is within the specified range
    return (value >= max) ? max : (value <= min) ? min : value;
}

// Reset the PID controller to its initial state
void Controller_Reset(PIDController *pid) {
    pid->I = 0.0f;
    pid->state_old = 0.0f;
    pid->state_f = 0.0f;
}

// Enable the PID controller
void Controller_Enable(PIDController *pid) {
    pid->enabled = true;
}

// Disable the PID controller
void Controller_Disable(PIDController *pid) {
    pid->enabled = false;
}

// Update the PID controller output based on the current state and setpoint
float Controller_Update(PIDController *pid, float set, float state, Mode ControllerType) {

    if (pid->enabled) {

        float e = set - state;  // Calculate the error between the setpoint and the current state

        // Declare variables for proportional, integral, and derivative terms
        float P, D, U_out, U_sat;

        switch (ControllerType) {
            case P_Cont:
                // Proportional control only
                return sat(pid->kp * e, pid->U_max, pid->U_min);

            case PI_Cont:
                // Proportional-Integral control
                P = pid->kp * e;
                U_out = P + pid->ki * pid->I;
                U_sat = sat(U_out, pid->U_max, pid->U_min);

                // Anti-windup using clamping method: Integrate only if the controller does not saturate and both error and controller output having opposite sign
                if (U_out == U_sat || e * U_out <= 0) {
                    pid->I += e * pid->dt;
                }
                return U_sat;

            case PID_Cont:
                // Proportional-Integral-Derivative control
                P = pid->kp * e;

                // Low pass filter on state
                pid->state_f = LPF(state, pid->fc, pid->dt, pid->state_f);

                // Calculate the derivative term of the state instead of the error to overcome the problem of derivative kick
                D = pid->kd * ((pid->state_f - pid->state_old) / pid->dt);

                // Update state variables
                pid->state_old = pid->state_f;

                // Calculate the output of the controller
                // Note: Taking the derivative term negative because it's the derivative of the state, not the error term
                U_out = P + pid->ki * pid->I - D;

                // Saturate the controller output to stay within the specified bounds
                U_sat = sat(U_out, pid->U_max, pid->U_min);

                // Anti-windup using clamping method: Integrate only if the controller does not saturate and both error and controller output having opposite sign
                if (U_out == U_sat || e * U_out <= 0) {
                    pid->I += e * pid->dt;
                }
                return U_sat;

            default:
                return 0;  // Default to return the saturated output
        }
    }

    return 0;  // Return 0 if the controller is disabled
}



void gyro_calibration(){
  for(uint16_t i=0; i<500; i++){
    mpu.getEvent(&a, &g, &temp);
    imu.gyro.bx += g.gyro.x;
    imu.gyro.by += g.gyro.y;
    imu.gyro.bz += g.gyro.z;
    delay(10);
  }
  imu.gyro.bx = imu.gyro.bx/500;
  imu.gyro.by = imu.gyro.by/500;
  imu.gyro.bz = imu.gyro.bz/500;
  imu.pitch=0;
  imu.roll=0;
}



void actuator_movements_curr()
{
  current.aft=-1*rs*sinf(DEG_TO_RAD*(imu.roll));
  current.forward=rs*sinf(DEG_TO_RAD*(imu.roll));
  current.lateral=rs*sinf(DEG_TO_RAD*(imu.pitch));
}
void actuator_movements_req()
{
  required.aft=-1*rs*sinf(DEG_TO_RAD*roll_req);
  required.forward=rs*sinf(DEG_TO_RAD*roll_req);
  required.lateral=rs*sinf(DEG_TO_RAD*pitch_req);
}

// ... (existing code)

////////////////////////////////////////////////////////////////////////PID CONTROLLER//////////////////////////////////////////////////////////////////////////////////////////////


////////////////////////////////////////////////////////////////////////PID CONTROLLER//////////////////////////////////////////////////////////////////////////////////////////////

// ... (existing code)




////////////////////////////////////////////////////////////////////////MAIN//////////////////////////////////////////////////////////////////////////////////////////////

void setup(void) {
  // put your setup code here, to run once:
  int c=0;
 

  Controller_Enable(&ControlLateral);
  Controller_Enable(&ControlAft);
  Controller_Enable(&ControlForward);
  
  Serial.begin(115200);
  Serial.println("Adafruit MPU6050 test!");
  
  // Try to initialize!
  if (!mpu.begin()) {
    Serial.println("Failed to find MPU6050 chip");
    while (1) {
      delay(10);
    }
  }
  aft.setSpeed(-255);
  forward.setSpeed(-255);
  lateral.setSpeed(-255);
  delay(5000);
  
  mpu.setAccelerometerRange(MPU6050_RANGE_2_G);

  mpu.setGyroRange(MPU6050_RANGE_500_DEG);

  mpu.setFilterBandwidth(MPU6050_BAND_10_HZ);

  Serial.println("");
  gyro_calibration();
  double MPUOffsets[6] = { -2776.00, -4439.00  ,1605.00, 91, 11, 6 };
//-2681.00  -4437.00  1592.00
  accelgyro.setXAccelOffset(MPUOffsets[0]);
  accelgyro.setYAccelOffset(MPUOffsets[1]);
  accelgyro.setZAccelOffset(MPUOffsets[2]);
  float rollbias=0,pitchbias=0;
  //

  
  delay(100);
  Serial.println("starting");
  aft.setSpeed(255);
  forward.setSpeed(255);
  lateral.setSpeed(255);
  delay(1400);
  aft.setSpeed(0);
  forward.setSpeed(0);
  lateral.setSpeed(0);
}
#define SIN_FREQ 0.3 // Frequency of the sinusoidal motion in Hz
#define AMPLITUDE 10 // Amplitude of the sinusoidal motion in degrees

// Function to generate sinusoidal desired roll and pitch values
void generateSinusoidalDesiredValues(float &roll, float &pitch) {
  // Calculate the current time in seconds
  float t = millis() / 1000.0;

  // Calculate the desired roll and pitch values using sine function
  // Adjust the frequency and amplitude as needed
  roll = AMPLITUDE * sin(2 * PI * SIN_FREQ * t);
  pitch = AMPLITUDE * sin(2 * PI * SIN_FREQ * t + PI / 2); // 90 degrees phase shift for pitch
}
void loop() {
  // put your main code here, to run repeatedly:
  unsigned long startTime = micros();
  /////////////////////////////////roll pitch/////////////////////////////////////////////////////////////////

  mpu.getEvent(&a, &g, &temp);

  //standard
  accelgyro.getMotion6(&ax, &ay, &az, &gx, &gy, &gz);
  imu.accel.x = static_cast<double>(ax) / 16384.0*9.6;
  imu.accel.y = static_cast<double>(ay) / 16384.0*10.1;
  imu.accel.z = static_cast<double>(az) / 16384.0*9.7;
  
  /////////////////////// GYROOOOOOO/////////////////////////////////////
  imu.gyro.x=(g.gyro.x-imu.gyro.bx/200)* 180 / PI;
  imu.gyro.y=(g.gyro.y-imu.gyro.by/200)* 180 / PI;
  imu.gyro.z=(g.gyro.z-imu.gyro.bz/200)* 180 / PI;
  
  imu.pitch_acc =  (atan2((imu.accel.y),sqrt(pow((imu.accel.x), 2) + pow((imu.accel.z), 2))) * 180 / PI);
  imu.roll_acc =  (atan2(-1 * (imu.accel.x) ,sqrt(pow((imu.accel.y), 2) + pow((imu.accel.z), 2))) * 180 / PI);


  imu.roll= alpha*(imu.roll+imu.gyro.x*dt)+(1-alpha)*(imu.roll_acc);
  imu.pitch= alpha*(imu.pitch+imu.gyro.y*dt)+(1-alpha)*(imu.pitch_acc);
  if(c<200)
  {
    c++;
    imu.pitch_bias+=imu.pitch;
    imu.roll_bias+=imu.roll;
    imu.gyro.bx+=g.gyro.x;
    imu.gyro.by+=g.gyro.y;
    imu.gyro.bz+=g.gyro.z;
  }

  else
  {
//    Serial.print("ROLL: ACC:");
//    Serial.println(imu.roll_acc-imu.roll_bias/200);
//    Serial.print(", PITCH: ACC:");
//    Serial.println(imu.pitch_acc-imu.pitch_bias/200);
//    generateSinusoidalDesiredValues(pitch_req,roll_req);
    imu.roll_acc=imu.roll_acc-imu.roll_bias/200;
    imu.pitch_acc=imu.pitch_acc-imu.pitch_bias/200;
    actuator_movements_curr();
    actuator_movements_req();

  aft.setSpeed(-1*Controller_Update(&ControlAft,required.aft,current.aft,PID_Cont));
  forward.setSpeed(-1*Controller_Update(&ControlForward,required.forward,current.forward,PID_Cont));
  lateral.setSpeed(-1*Controller_Update(&ControlLateral,required.lateral,current.lateral,PID_Cont));


  Serial.print(imu.roll);
//   Serial.print("   , pitch : ");
  Serial.print(",");

  Serial.println(imu.pitch);
  }
    



  
//  actuator_movements_required();
  delay(4);

  unsigned long endTime = micros();
  float elapsedTime = float(endTime - startTime);
  dt= (elapsedTime)/1000000.0f;
//  Serial.println(dt,6);
}
